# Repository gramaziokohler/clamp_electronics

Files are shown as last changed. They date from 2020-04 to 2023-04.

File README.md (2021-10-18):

# clamp_electronics
Electronics for remote controlled robotic actuators (clamps). 

This repo is part of the [Robotic Assembled Timber Structures with Integral Timber Joints](https://github.com/gramaziokohler/integral_timber_joints) project. 

## Repo folder structure

This repository hold the following files:

- **/xx_Description** - Eagle schematics and board designs for a specific controller design
- **/eagle_library** - stores custom eagle libraries from third-party or created by myself
- **/doc** - Electronics modules and other components documentation from original manufactures.

## Design Goals

The goal of the clamp controller is to be able to achieve the following high-level functions: 

- Communicate wirelessly with a radio base station
  - Receive commands
  - Report status
  - Report a jammed stop during move
- Control 1 or 2 motors for the clamp's main linear movement
  - Positional Control
  - Follow a trapezoidal motion profile
- Operate on 3 or 4-cell Li-Po Battery power
- Monitor jamming conditions of the clamp
- Monitor sensors (if any, such as loadcells)
- Monitor end / homing switch
- Monitor pneumatic autoswitch
- Monitor battery voltage

## Controller Design

Not all designs implemented the full list of design goals.

### [01_SerialController](/01_SerialController/01_SerialController.md)

This controller receives command from Serial Tx Rx pins.

Two load cell can be connected via two HX711 Analog-to_Digital Module.

The design supports two DC motors with *single* channel encoder. The shaft rotation direction is inferred from the direction of programmed movement. (This design is later proved to be imprecise)

### [02_RadioPIDController](02_RadioPIDController/02_RadioPIDController.md)

This controller interfaces the CC1101 radio directly via Hardware SPI on Arduino Nano. It can receive and respond to commands from either USB Serial or from the Radio.

The hardware and pin out supports two motors being PID controlled with two-channel encoder feedback.

### [03_RadioPIDControllerV2](03_RadioPIDControllerV2/03_RadioPIDControllerV2.md)

This controller is an improvement of the 02_RadioPIDController with the intent to improve the following aspects:

- Better DC power regulation to avoid digital blackout
- Ability to support a two-motor firmware or single-motor (with added features) firmware.
- 1 or 2 LED output with onboard series resistor

### [10_ESP32CAMAdapter](10_ESP32CAMAdapter/10_ESP32CAMAdapter.md)

This an adapter board for connecting AIThinker ESP32-CAM module.

## Sub-systems and Electronic Module Documentation

### Motor Driver

[Motor Driver XY160D](doc/motor_driver/motor_driver_XY160D.md)

This H-Bridge Bi-Directional MOSFET motor driver is chosen due to its high rated current (7A constant, 50A peak).  

- Other drivers such as L298N offers low output current (L298N only 2A constant output 3A peak per channel) 
- This driver has a simple IN1 + IN2 + ENA interface which is easy to interface. 
- PWM and Bidirectional operation is necessary for position control.

### Radio

[Details of CC1101 Radio Module](doc/radio/CC1101_Radio.md)

This CC1101 radio module is chosen because it is the most available sub-GHz packet based radio.

- The sub-GHz frequency is better at going around obstacles in a construction environment.
- ISM bands that are free to use.
- The highly integrated radio transceiver chip on a module is easy to use and interface. 
- Existing Arduino compatible library exists.

Radio frequency / channel / sync word and it's operation is controlled by software and are documented in firmware repo.

### MCU

The Arduino Nano (ATmega328 + new bootloader) is chosen for its small size, low cost and protoboard friendly pin layout. The Nano do not have a lot of IO available but is barely enough for a 2 motor controller.

[Arduino Nano V3 Pinout](http://lab.dejaworks.com/arduino-nano-pinouts/) ( [Arduino.cc Nano Page](https://store.arduino.cc/arduino-nano) )

### Load Cell

A 4-wire load cell can be used to dynamically measure the pull force of the actuator. Such load cell can be interfaced to the Arduino via a AD Converter designed for load cell measurement.

[Details of the HX711 Load Cell A/D Module](/doc/load_cell/load_cell.md)

The HX711 module was selected due to its compact size, low cost and ready-to-use library. Measuring frequency is 80Hz.

### Battery Voltage Regulation for controller

The fluctuating battery voltage for a 4-cell Li-Po is between 12.8V to 16.8V. This needs to be regulated to stable 5V DC for the digital circuitry.

[Details and calculation of LM7805 option](doc/voltage_regulation/linear_regulator.md)

### Battery Voltage Sense

[Details and calculation of voltage divider](doc/battery_sense/Battery_Voltage_Sensing.md)

### Battery Cable Harness

A Y cable is necessary to connect the Li-Po Battery to both the motor driver and the controller Battery. 

**Male XT60 Connector** at the battery side

**2x Female Phoenix Terminal Block Plug** (Phoenix 1757019 - MSTB 5.08 picth) at controller side.

------

## Peripheral Devices

The choice of DC motor and Li-Po Battery is flexible from the perspective of the controller electronics. As long as their specification is within allowable range defined below:

### DC Motor

The chosen DC motor should be rated 12V. Other ratings might work as long as overheat is not an issue and sufficient torque is produced.

### Hall Effect Sensor

Two phase hall effect shaft encoder should be used for positional feedback. The output of the encoder should ideally be 5V TTL logic. 

Should the motor have a gearbox, the shaft encoder should be attached to the motor shaft (not the gearbox output shaft) for better resolution.

Sensor resolution should be around 500 - 1000 steps per 1mm clamp linear output.

### Li-Po Battery

**4-cell** Li-Po battery is chosen for the following reasons:

- High power density for starting DC motor
- High energy density to save space and weight
- 14.8V - 16.8V voltage match well with 12V DC motor.

**1000mAh** or above for reasonable use time.

**XT60 Connector** is conventional

**Voltage Assumption for calculation**: We assume a fully charged 4-cell battery to have **16.8V (@4.2V)**, and stop using the battery at **14.8V (@3.7V)**  , although absolute minimum is **14.0V (@3.5V)**

Note: 3-cell battery will also operate fine but at reduced torque

Credits
-------------

This repository was created by Pok Yin Victor Leung <leung@arch.ethz.ch> [@yck011522 ](https://github.com/yck011522) at [@gramaziokohler](https://github.com/gramaziokohler)

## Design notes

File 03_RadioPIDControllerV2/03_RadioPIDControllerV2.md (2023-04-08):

# 03 Radio PID Controller V2

This controller is an upgrade of 02_Radio_PID_Controller and retains most of the design features of the previous controller with the following modifications:

- 5V power regulation is improved 
- LED connections and resistors are integrated
- Some bottom routing is redesigned for easier soldering.

## Design Goals

This clamp controller can achieve the following goal (with proper firmware):

- Control and communicate through CC1101 radio module. (SPI)
- Control 1 or 2 motors for the clamp's main linear movement
  - PWM / Bidirectional output via XY160D driver to two DC motors
  - Close loop feedback from two-phase hall effect shaft encoder from 2 motors
- Operate on 3 or 4-cell Li-Po Battery power
- Monitor homing switch / pneumatic autoswitch
- Monitor battery voltage
- Output for 1 or 2 LED status light

## Component choice

**Battery Choice:** Up to user (typical: 4-cell Li-Po 1000mAh 4S 75C)

**Radio Choice:** [CC1101 Module](../doc/radio/CC1101_Radio.md)

**Motor Driver Choice:** [Motor Driver XY160D](../doc/motor_driver/motor_driver_XY160D.md)

**MCU Choice:** Arduino Nano (ATMEGA328 with new bootloader)

**Voltage Regulation:** Single stage LM7805 solution (see schematic)

**Addressing / Settings DIP Switch:** 4 position DIP switch with resistor ladder

**End Switch Choice:** Normal close (NC) switch

## Schematic

[Eagle Schematic File](Controller.sch)

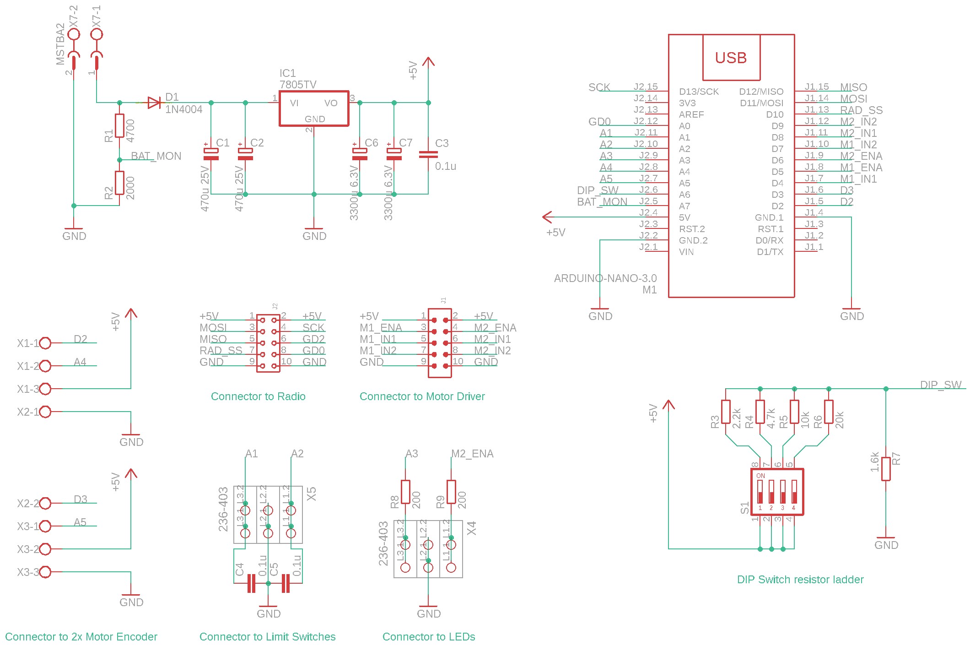
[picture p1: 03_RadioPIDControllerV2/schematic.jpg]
schematic


## Board

This board is built on **protoboard**, the following board shows mostly the hard wiring underneath the protoboard. There are jumpers that routes from top side not drawn here.

[Eagle Board File](Controller.brd)

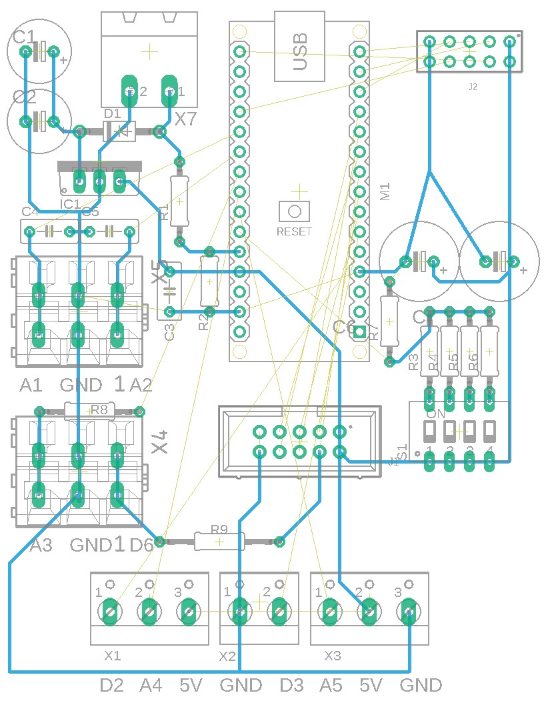
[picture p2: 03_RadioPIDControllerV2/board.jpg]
board


## Photo

The Controller in enclosed case with plugged in battery. The disconnected cables goes to DC motor with encoder.

Photo_WithCoverTop

------

Arduino Nano and radio module (Blue PCB with antenna) on protoboard. The Motor driver (red PCB) can be  seen below the protoboard. 

Photo_OffCover

## Arduino Pin Assignment

| | 1 motor operation | 2 motor operation |
| --- | --- | --- |
| Homing Switch | 1 switch (A1) | 2 switches (A1, A2) |
| Gripper Autoswitch | 1 input (A2) | not available |
| Motor Encoder 1 | interrupt (D2) | interrupt (D2, D3)  |
| Motor Encoder 2 | interrupt (D3) | gpio (A4, A5) |
| Motor Status LED (orange/red) | D6 | not available |

## Modification

During the third phase of the project the power regulation is modified. The LM7805 is removed and a LM2596 DC-DC converter module is placed in the same role.  This improved the regulation efficiency during standby mode and particularly important with the addition of the ESP32 CAM module. The ESP32 CAM draws substantial current and (confirmed by test) cannot be supported by the 7805, causing it to run into thermal protection. 

| Device | Current Draw @14.8V (LM7805) | Current Draw @14.8V (LM2596) |
| --- | --- | --- |
| Controller with No Radio | 0.055 | 0.1 |
| Controller with Radio | 0.056 | 0.116 |
| + ESP32 CAM | 0.1 | 0.23 |
| + ESP32 CAM LED On | 0.15 | 0.358 |

The new LM2596 module is not integrated to the same PCB but is wired off-board and is fixed with foam tape to the side of the worm gearbox.

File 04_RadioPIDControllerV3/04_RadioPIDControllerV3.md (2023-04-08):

# 04 Radio PID Controller V3

This controller is an upgrade of 03_Radio_PID_Controller and retains most of the design features of the previous controller with the following modifications:

- Arduino Mega 2560 PRO from robotdyn
- 1 channel Main Motor Control
- 2 channels Motor Control for gripper motors
- PCB base instead of hand-soldered 

## Design Goals

This clamp controller can achieve the following goal (with proper firmware):

- Control and communicate through CC1101 radio module. (SPI)
- Control 3 motors, 1 for the clamp's main linear movement, 2 for clamp gripper actuation
  - PWM / Bidirectional output via XY160D driver to two DC motors
  - Close loop feedback from two-phase hall effect shaft encoder from 2 motors
  - Main motor and gripper motor not not operate simultaneously. 
- Operate on 3 or 4-cell Li-Po Battery power
- Monitor homing switch / pneumatic autoswitch
- Monitor battery voltage
- Output for 1 or 2 LED status light

## Component choice

**Battery Choice:** Up to user (typical: 4-cell Li-Po 1600mAh 4S 75C)

**Radio Choice:** [CC1101 Module](../doc/radio/CC1101_Radio.md)

**Motor Driver (Main Screw Motor) Choice:** H-Bridge Motor Driver JZ3615 (15A continuous, 50A peak)

**Motor Driver (Pin Gripper Motor) Choice:** [H-Bridge Motor Driver L298HN](https://www.sparkfun.com/datasheets/Robotics/L298_H_Bridge.pdf) (Total 4A continuous)

**MCU Choice:** Arduino Nano (ATMEGA328 with new bootloader)

**Voltage Regulation:** Single stage LM7805 solution (see schematic)

**Addressing / Settings DIP Switch:** 4 position DIP switch with resistor ladder

**End Switch Choice:** Normal close (NC) switch

## Schematic

[Eagle Schematic File](Controller.sch)

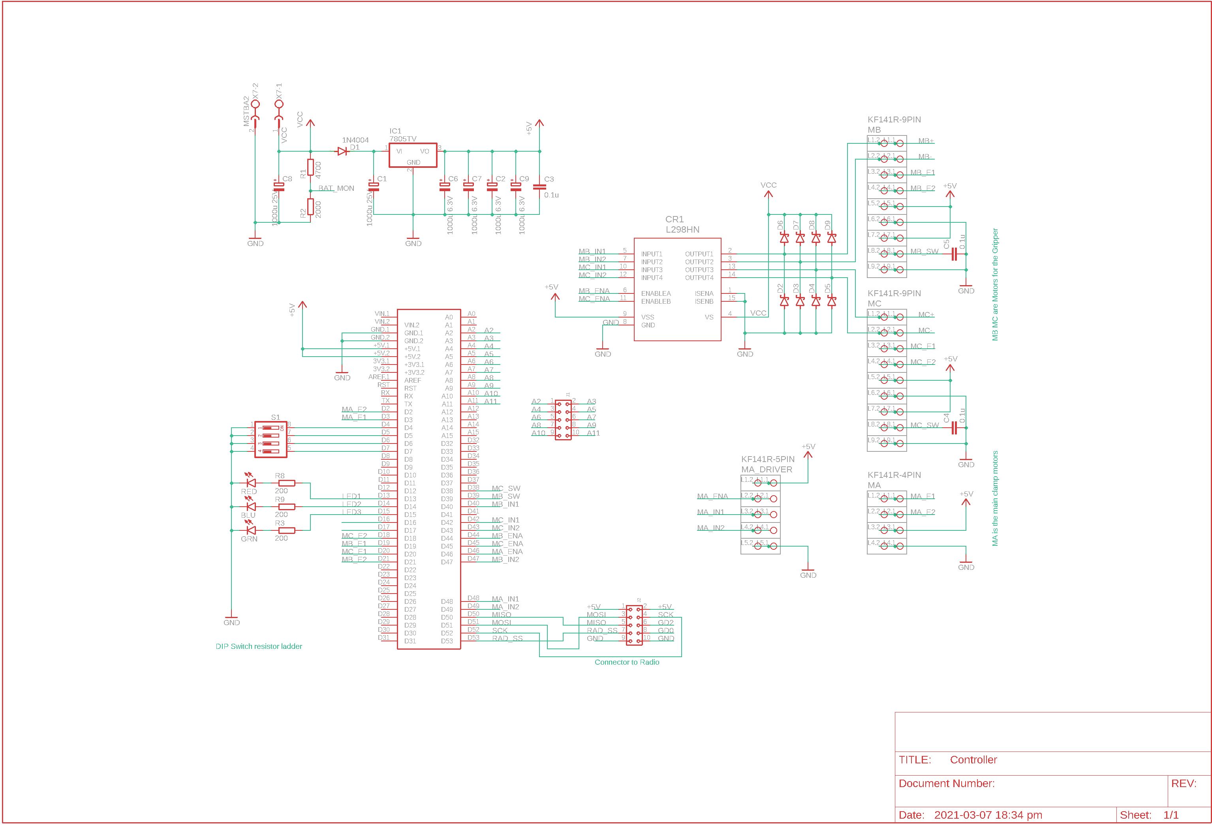
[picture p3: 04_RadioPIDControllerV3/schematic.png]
schematic


## Board

This board is built by PCB fab company in China, the following drawing shows bottom side (blue) and top side (red).

[Eagle Board File](Controller.brd)

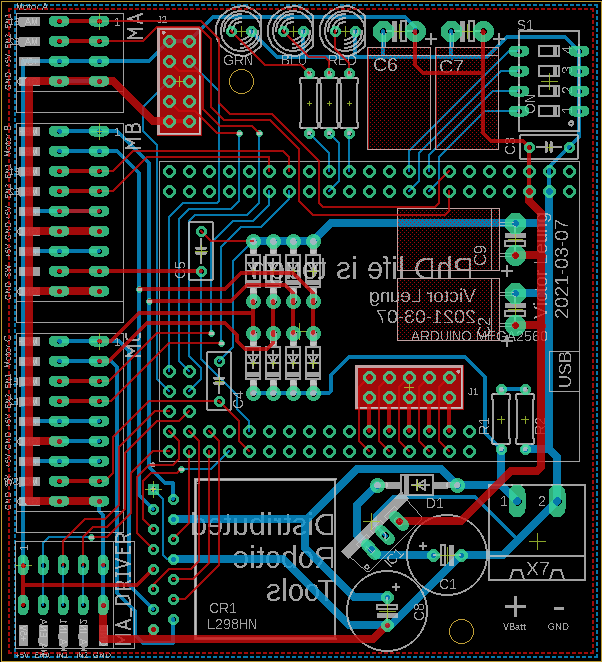
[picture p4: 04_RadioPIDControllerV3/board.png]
board


## Errata

- **BAT_MON** net should be connected to an Analog Pin on the MCU, but was not connected. This is rectified by jumper wire from trace between R1 R2 to J1 Pin **A3**.
-  **GD0** net (radio message arrive flag) should be connected to a pin on the MCU, but was not connected. This is rectified by jumper wire from J2 GD0 pin to J1 Pin **A2**.
-  Two buttons are added for manually controlling the grippers, they are wired to A96 A10 A11 

## Photo

The Controller in enclosed case with all cables connected.

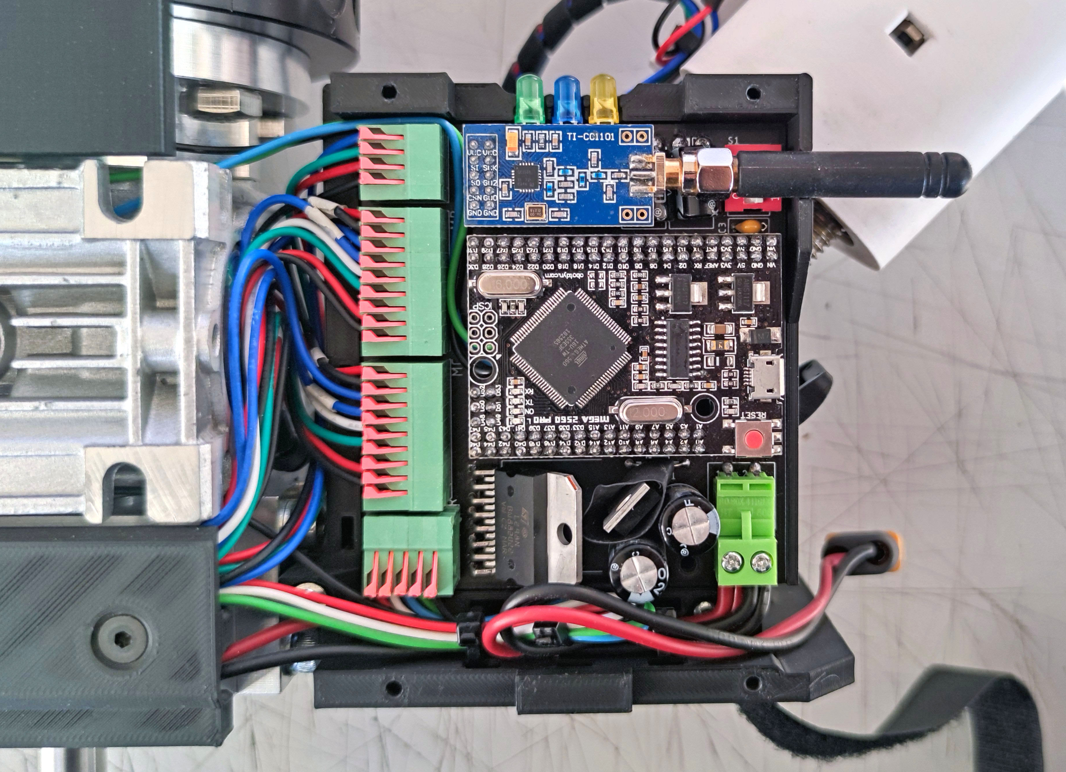
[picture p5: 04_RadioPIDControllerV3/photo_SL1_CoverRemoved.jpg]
photo_SL1_CoverRemoved


------

## Arduino Pin Assignment

| | MA (Screw Motor) | MB (Gripper Motor) | MC (Gripper Motor) |
| --- | --- | --- | --- |
| Motor IN1 | MA_IN1 (D48) | MB_IN1 (D40) | MC_IN1 (D42) |
| Motor IN2 | MA_IN2 (D49) | MB_IN2 (D47) | MC_IN2 (D43) |
| Motor Enable | MA_ENA (D46) | MB_ENA (D44) | MC_ENA (D45) |
| Motor Encoder 1 | MA_E1 (D2) interrupt 4 | MB_E1 (D19) interrupt 2 | MC_E1 (D20) interrupt 1 |
| Motor Encoder 2 | MA_E2 (D3) interrupt 5 | MB_E2 (D21) interrupt 0 | MC_E2 (D18) interrupt 3 |
| Homing Switch | nil | MB_SW (D39) | MC_SW(D38) |

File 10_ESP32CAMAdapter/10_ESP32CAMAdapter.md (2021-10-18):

# 10_ESP32CAMAdapter

This an adapter board for connecting AIThinker ESP32-CAM module.

The Camera Module draws power from the stabilized 5V supply of the Clamp controller. It does not communicate directly with the clamp controller. 

- A DIP switch is used to set the IP address of the Controller. 
- A Status LED indicates successful connection with the Wi-Fi Access Point.

The board is implemented on protoboard. The wire terminal is not present and is replaced with a directly soldered wire. The board have to be removed during programming. 

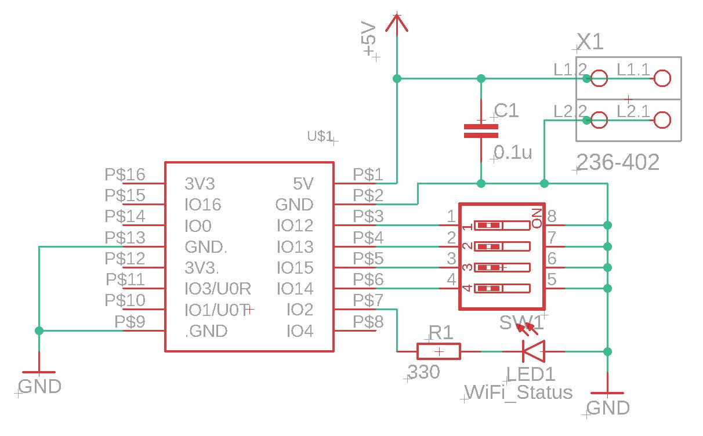
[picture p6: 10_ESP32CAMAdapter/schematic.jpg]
schematic


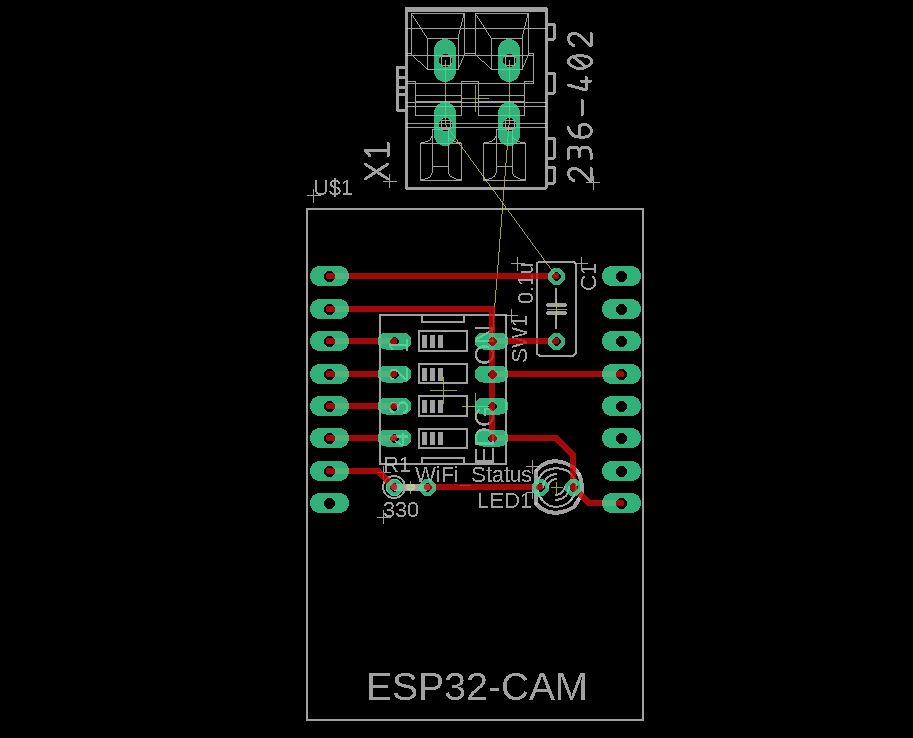
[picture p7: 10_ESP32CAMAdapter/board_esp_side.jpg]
board_esp_side


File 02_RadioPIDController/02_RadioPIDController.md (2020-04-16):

# 02 Radio PID Controller

This controller is put together in a rush for project Tokyo. Some components are drawn here, but not installed due to lack of on-hand components.

## Design Goals

This clamp controller can achieve the following goal (with proper firmware):

- Control and communicate through CC1101 radio module. (SPI)
- Control 1 or 2 motors for the clamp's main linear movement
  - PWM / Bidirectional output via XY160D driver to two DC motors
  - Close loop feedback from two-phase hall effect shaft encoder from 2 motors
- Operate on 3 or 4-cell Li-Po Battery power
- Monitor end / homing switch
- Monitor battery voltage
- Output for a LED status light or buzzer 

## Component choice

**Battery Choice:** Up to user (typical: 4-cell Li-Po 1000mAh 4S 75C)

**Radio Choice:** [CC1101 Module](../doc/radio/CC1101_Radio.md)

**Motor Driver Choice:** [Motor Driver XY160D](../doc/motor_driver/motor_driver_XY160D.md)

**MCU Choice:** Arduino Nano (ATMEGA328 with new bootloader)

**Voltage Regulation:** Single stage LM7805 solution (see schematic)

**Addressing / Settings DIP Switch:** 4 position DIP switch with resistor ladder

**End Switch Choice:** Normal close (NC) switch

## Schematic

[Eagle Schematic File](Controller.sch)

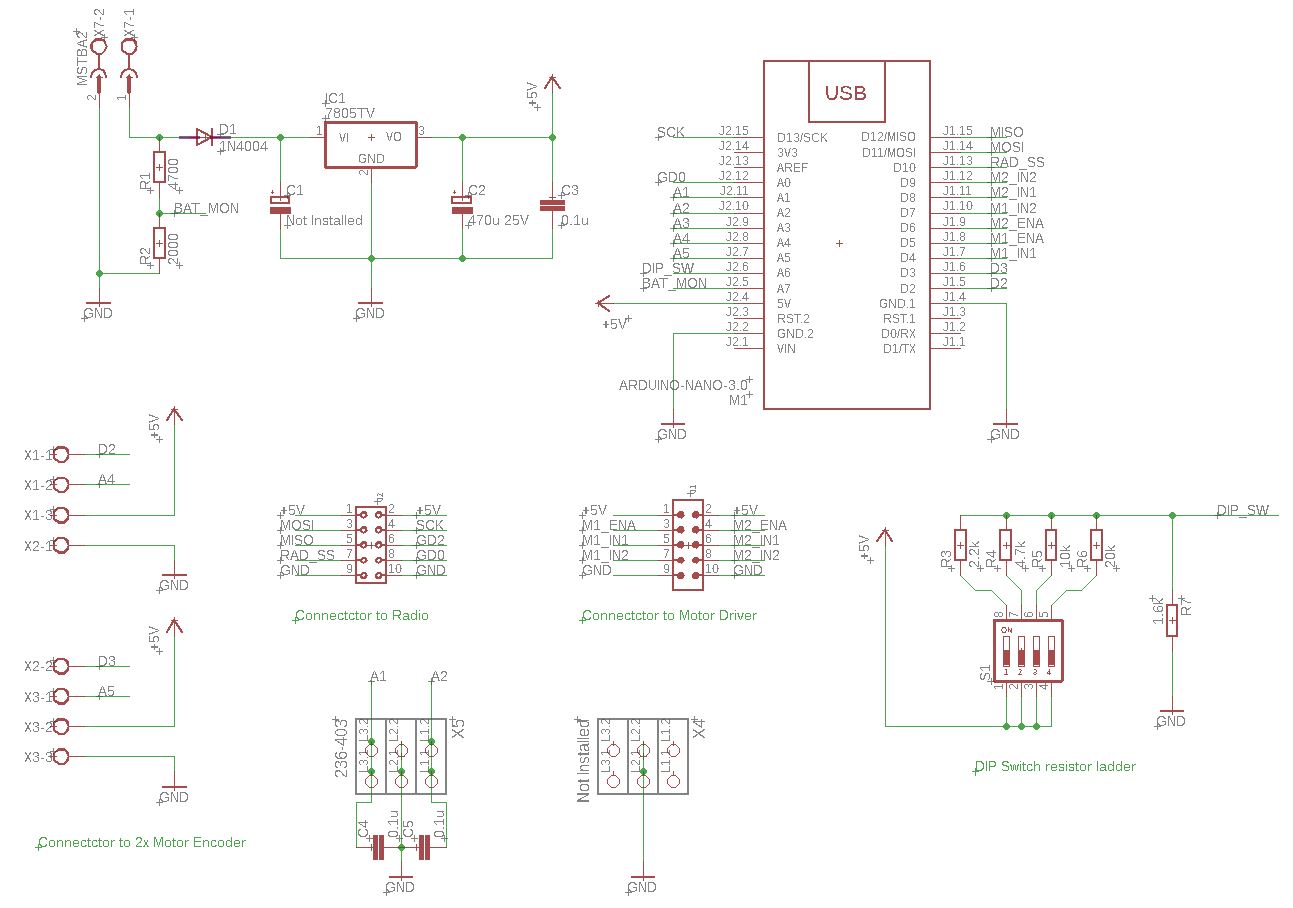
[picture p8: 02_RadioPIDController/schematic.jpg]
schematic


## Board

This board is built on **protoboard**, the following board shows mostly the hard wiring underneath the protoboard. There are jumpers that routes from top side not drawn here.

[Eagle Board File](Controller.brd)

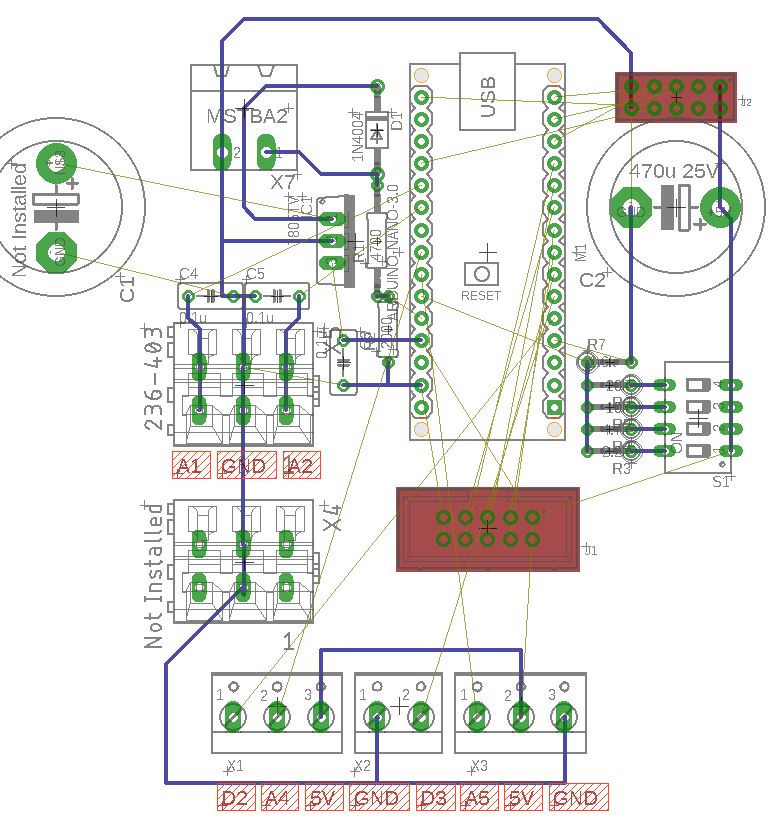
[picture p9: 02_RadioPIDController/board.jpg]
board


## Photo

The Controller in enclosed case with plugged in battery. The disconnected cables goes to DC motor with encoder.

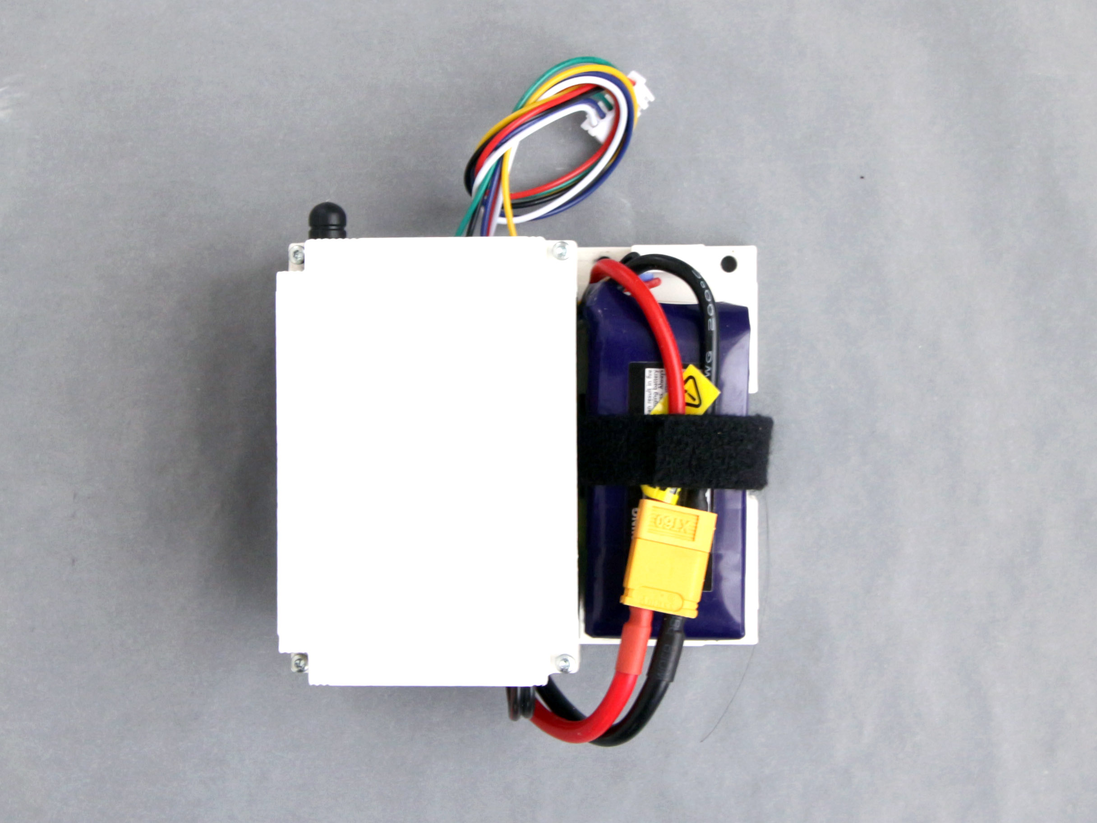
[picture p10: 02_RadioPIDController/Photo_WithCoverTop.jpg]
Photo_WithCoverTop


------

Arduino Nano and radio module (Blue PCB with antenna) on protoboard. The Motor driver (red PCB) can be  seen below the protoboard. 

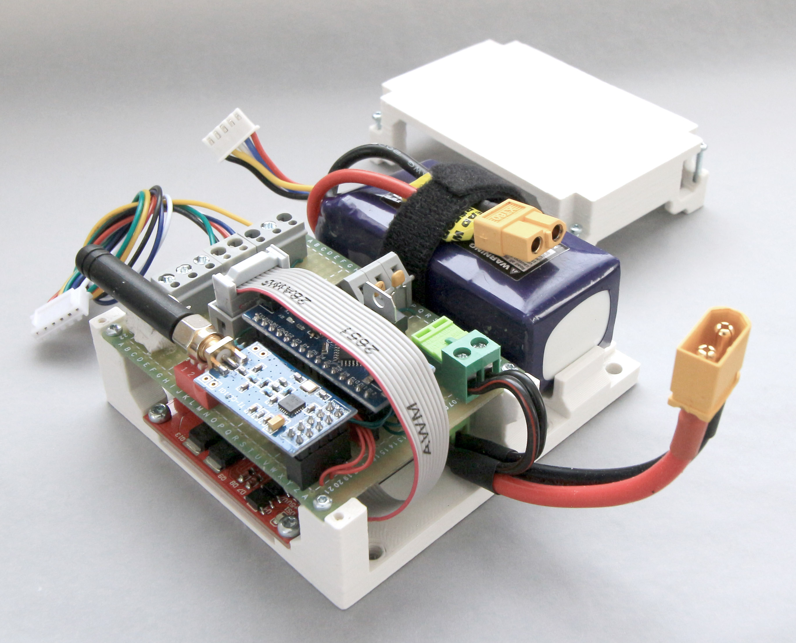
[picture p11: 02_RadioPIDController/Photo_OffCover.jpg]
Photo_OffCover


## Arduino Pin Assignment

The following header file can be used for pin assignment

(TODO)

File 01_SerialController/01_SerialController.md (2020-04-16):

# 01 Serial Controller

## Design Goals

This clamp controller can achieve the following goal (with proper firmware):

- Control and communicate through serial interface. 
  - From computer via **CH340 USB chip** on Arduino Nano
  - From Radio via **TX RX interface** with [USB Radio Dongle](../00_USBRadioDongle/00_USBRadioDongle.md)
- Control 1 or 2 motors for the clamp's main linear movement
  - PWM / Bidirectional output via XY160D driver to two DC motors
  - Close loop feedback from single-phase hall effect shaft encoder from 2 motors
- Operate on 3 or 4-cell Li-Po Battery power
- Monitor battery voltage

## Component choice

**Battery Choice:** Up to user (typical: 4-cell Li-Po 1000mAh 4S 75C)

**Radio Choice:** [00_USBRadioDongle](../00_USBRadioDongle/00_USBRadioDongle.md)

**Radio Interface:** TX RX Interface with 5V power

**Motor Driver Choice:** [Motor Driver XY160D](../doc/motor_driver/motor_driver_XY160D.md)

**Load Cell Interface:** [HX711 AD Module](../doc/load_cell/load_cell.md)

**Load Cell Choice:** Up to user (any 4 wire load cell)

**MCU Choice:** Arduino Nano (ATMEGA328 with new bootloader)

**Voltage Regulation:** Single stage LM7805 solution (see schematic)

**End Switch Choice:** No end switch is connected. (end position inferred by software)

## Schematic

[Eagle Schematic File](SerialController.sch)

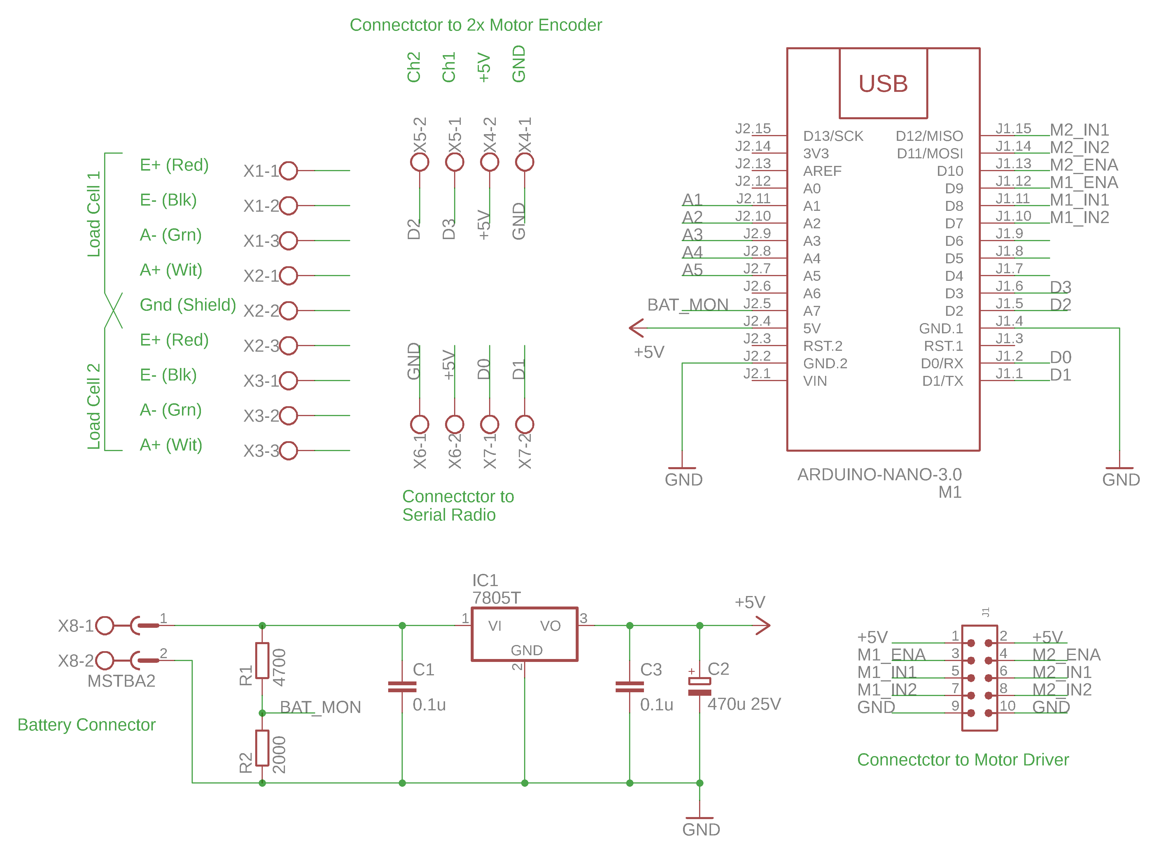
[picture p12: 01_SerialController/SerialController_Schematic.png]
SerialController_Schematic


## Photo

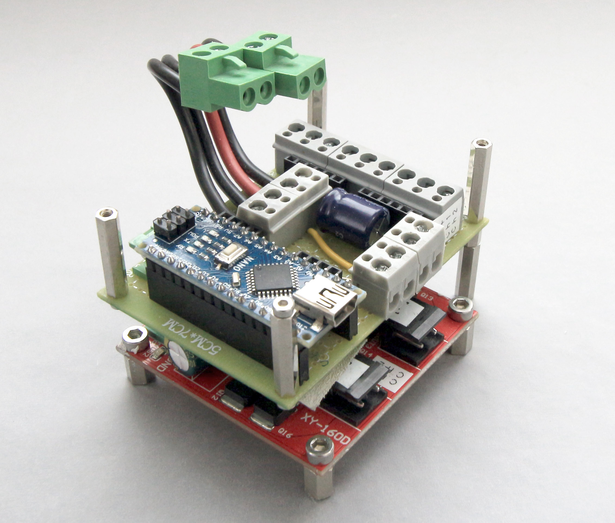
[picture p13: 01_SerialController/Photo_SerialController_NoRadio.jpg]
Photo_SerialController_NoRadio


## Test Notes

A simple test was performed to determine if the encoder has good repeatability. 

Result: Single-phase encoder is not reliable for bi-directional positional control. 

Inferring rotational direction is not reliable and result in poor axis repeatability.

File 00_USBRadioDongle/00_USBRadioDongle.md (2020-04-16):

# 00 USB Radio Dongle

This is a USB to CC1101 Radio dongle. 

[Details of CC1101 Radio Module and it's available frequency, mode and settings](../doc/radio/CC1101_Radio.md)

## Design Goals

This clamp controller can achieve the following goal (with proper firmware):

- Allow a PC to connect to it via USB. 
- Allow the PC to configure the CC1101 settings via the USB (address, frequency, channel and sync word)
- Allow the PC to send and receive variable length message packet via the USB
- Allow debug messages to be printed to a 1602 LCD Screen (via I2C bus with the PCF9574 IO Expander)

This radio is intended to be use as a **modular building block** for the network of remote-controlled clamps. It can be used on the master mode (PC) and the slave nodes (e.g. [01_SerialController](..\01_SerialController\01_SerialController.md)). However, later slave node controller (e.g. [02_RadioPIDController](..\02_RadioPIDController\02_RadioPIDController.md)) have integrated the radio control directly on the controller MCU, omitting the need for this dongle, saving an Arduino Nano and space. 

## Component choice

**Radio Choice:** [CC1101 Module](../doc/radio/CC1101_Radio.md)

**MCU Choice:** Arduino Nano (ATMEGA328 with new bootloader)

**Power:** Powered by host computer USB Port @ 5V

**Connector to 01 Serial Radio :** Phoenix Terminal Block Socket 5.08mm Pitch

**Connector to IC LCD Screen:** Reichelt PS Series 2.5mm Pitch 5 Pin PCB Connector (PS25/5G BR)  

## Schematic

[Original Eagle Schematic File](Dongle.sch)

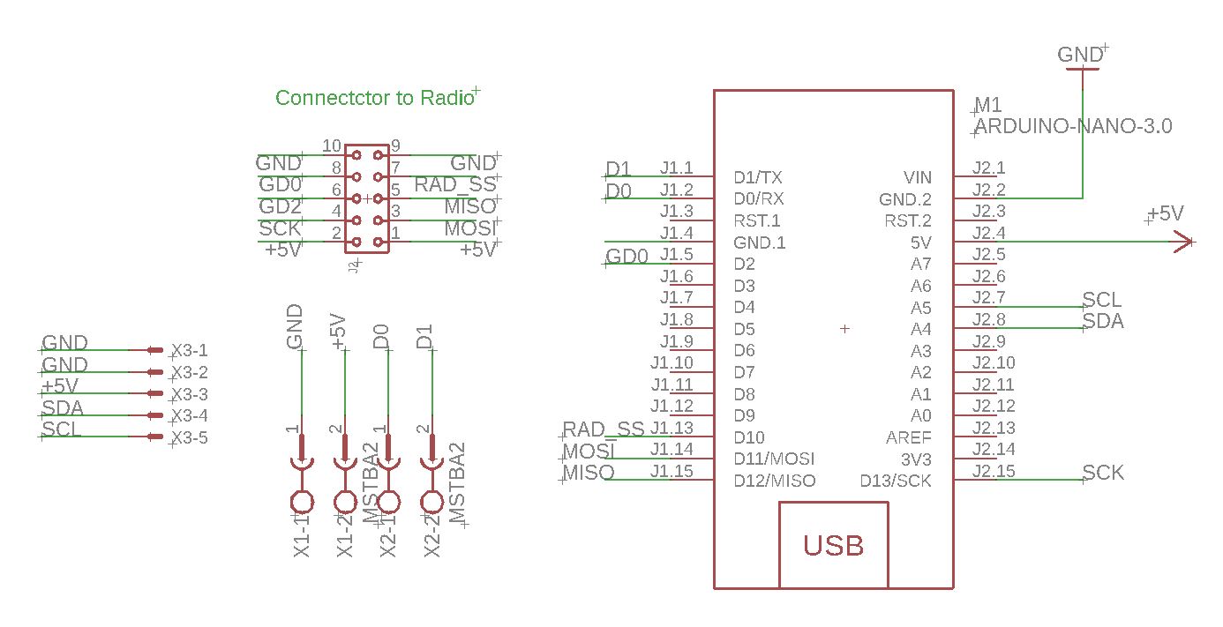
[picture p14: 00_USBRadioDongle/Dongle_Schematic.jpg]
Dongle_Schematic


## Board

This board is built on a 50mm x 70mm **protoboard**. The wiring is mainly completed using small wires. Arrangement of the components can refer to the photo below. The schematic drawing is also drawn with the connectors oriented the same as in the PCB.

## Photo

The Arduino Nano and CC1101 radio module can be seen. Mounted to a plastic case.

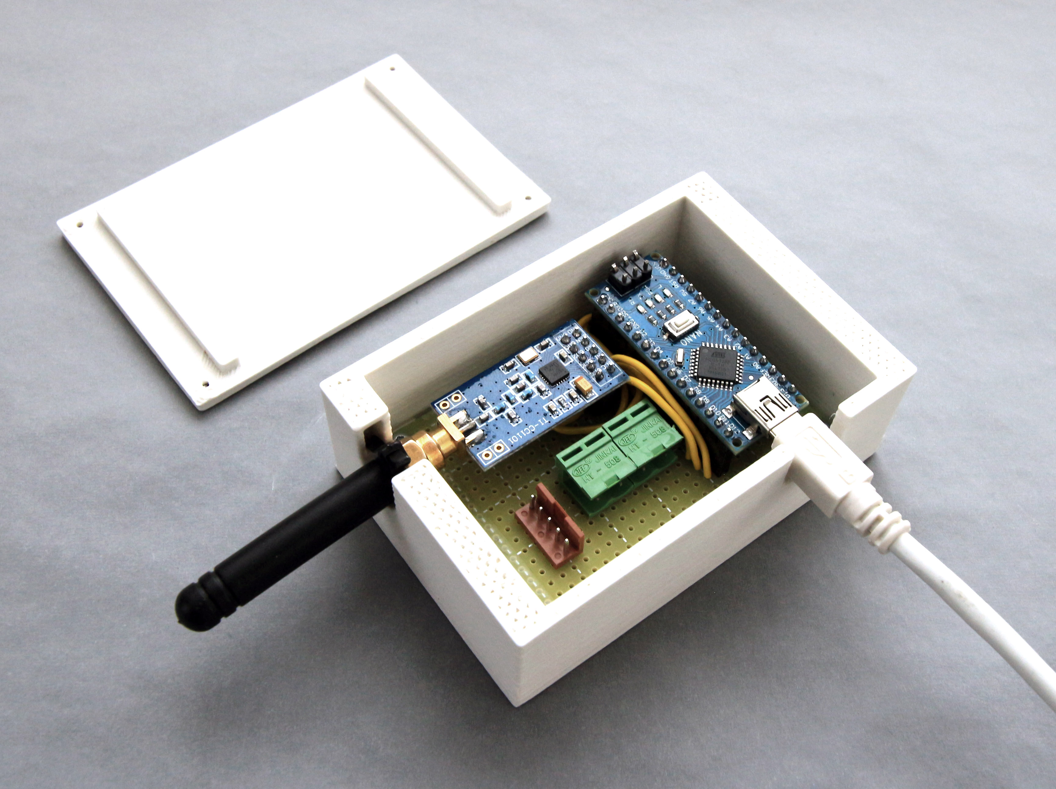
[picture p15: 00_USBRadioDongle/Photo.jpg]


------

Radio with case cover closed.

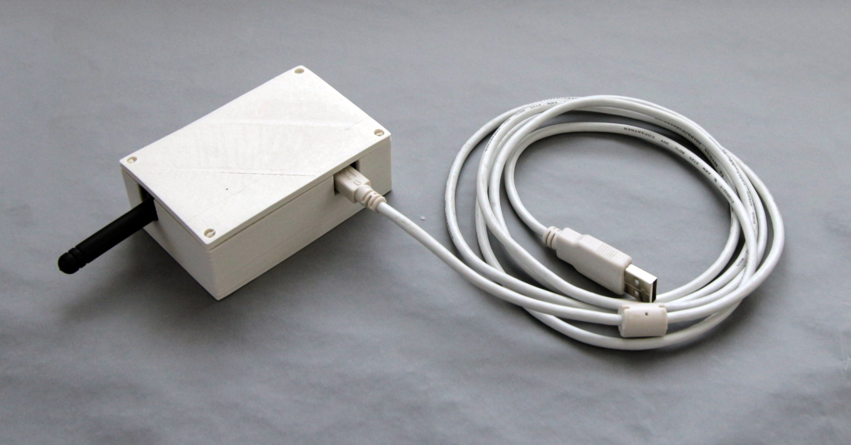
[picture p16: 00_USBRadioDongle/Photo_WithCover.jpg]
Photo_WithCover


## Firmware

Please see the serial_radio section in the [clamp_firmware repo](https://github.com/gramaziokohler/clamp_firmware).

## Arduino Pin Assignment

To the CC1101 radio module

| Radio Pin | Arduino Pin | Note |
| --- | --- | --- |
| 5V+ | 5V+ | |
| GND | GND | |
| CSN | D10 | Radio Slave Select |
| MOSI | D11 | MOSI Data |
| MISO | D12 | MISO Data |
| SCK | D13 | Serial Clock |
| GD0 | D2 | Message Arrival Indication |

------

To the dubug LCD screen

| LCD Screen Pin | Arduino Pin | Note |
| --- | --- | --- |
| Vcc | 5V+ | |
| GND | GND | |
| SDA | A4 | Serial Data  |
| SCL | A5 | Serial Clock |

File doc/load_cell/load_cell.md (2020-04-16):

# HX711 Load Cell A/D Module

There are different HX711 module on the market. Notably the Sparkfun version and this brand-less version. Note that pin arrangement is not identical. 

I choose this brand-less option simply because of lower cost.

HX711_module

## Specification of HX711

 [Data Sheet of Avia Semiconductor HX711](HX711.pdf)

**Resolution:** 24bit

**Measurement frequency:**10Hz / 60Hz (selectable)

## Pin Connection

Between Arduino and HX711 module:

| Label on module | Arduino Pin | Notes |
| --- | --- | --- |
| VCC | +5V | Power |
| GND | GND | Power |
| DT | Software SPI (Any IO Pin) | SPI Data  |
| SCK | Software SPI (Any IO Pin) | SPI Clock |

____

Between HX711 module and load cell:

| Label on module | Load Cell Wire | Cable Color (most of the time) |
| --- | --- | --- |
| E+ | Excitation + | Red |
| E- | Excitation - | Black |
| A- | Amplifier - | Green |
| A+ | Amplifier + | White |
| B- | Not Connected  | |
| B+ | Not Connected  | |
| GND | Shield | Wire or foil shield |

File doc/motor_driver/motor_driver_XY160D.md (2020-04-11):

# XY-160D motor driving board

**Motor Power Input Voltage** DC 6.5V - 27V

**Digital Power Input Voltage** DC 5V

**Number of Channels:** 2

**Max continuous output current:**  7A (Per Channel)

**Peak output current**: 50A

**PWM frequency range** 0-10 kHz (PWM signal at ENA input is used to regulate speed)

**Minimum pulse width:** 5us.

**Control signal Level (Compatible 3.3V/5V)**

**Logic High (H):** DC 3.0 ~ 6.5V

**Logic Low (L):** DC0 ~ 0.8V

| Pin Function | Label | Connection |
| --- | --- | --- |
| Drive Power Input +ve | 9-24V | Battery Positive |
| Drive Power Input -ve | PGND | Battery Negative |
| Power Output - Channel 1 +ve | OUT1 | Channel 1 Motor +ve |
| Power Output - Channel 1 -ve | OUT2 | Channel 1 Motor -ve |
| Power Output - Channel 2 +ve | OUT3 | Channel 2 Motor +ve |
| Power Output - Channel 2 -ve | OUT4 | Channel 2 Motor -ve |
| Digital Power Input +ve | +5V | Arduino 5V |
| Digital Power Input -ve | GND | Arduino Ground |
| Digital Input - Channel 1 - 1 | IN1 | Arduino GPIO |
| Digital Input - Channel 1 - 2 | IN2 | Arduino GPIO |
| Digital Input - Channel 2 - 1 | IN3 | Arduino GPIO |
| Digital Input - Channel 2 - 2 | IN4 | Arduino GPIO |
| Digital Input - Channel 1 Speed | ENA (near IN1) | Arduino GPIO (PWM)  |
| Digital Input - Channel 2 Speed | ENA (near IN3) | Arduino GPIO (PWM)  |

Note: Motor +ve and -ve denote when the motor spins according to Right Hand Rule. (a.k.a. CCW when viewed from output end.)

## Control Truth Table

| ENA  | IN1  | IN2  | OUT1 OUT2 Effect |
| ---- | ---- | ---- | --- |
| x | L | L | Short (Breaking) |
| x | H | H | Isolate |
| PWM  | H | L | Rotate (TODO: OUT1 > OUT2 ?) |
| PWM  | L | H | Rotate (TODO: OUT1 > OUT2 ?) |

## Connection to Motor 

Out 1 / Out 3 -> Motor +ve Lead

Out 2 / Out 4 -> Motor -ve Lead

## **Physical**

**PCB Size**  55x55x16mm  

**Mounting hole size**  3mm

**Weight** 32g

## Purchase

双路直流电机驱动板模块工业级马达正反转PWM调速L298逻辑7A160W

https://detail.tmall.com/item.htm?id=545415074433&spm=a1z09.2.0.0.32392e8dqyPg5S&_u=jl5jjmhde86 

## PDF

[XY160D_7A_160W_MotorDriver.pdf](XY160D_7A_160W_MotorDriver.pdf)

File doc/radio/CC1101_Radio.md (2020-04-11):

# CC1101 Radio Module

CC1101 is a [Low-power Sub-1 GHz wireless transceiver from Texas Instruments](http://www.ti.com/product/CC1101). 

> CC1101 is a low-cost sub-1 GHz transceiver designed for very low-power wireless applications. The circuit is mainly intended for the ISM (Industrial, Scientific and Medical) and SRD (Short Range Device) frequency bands at 315, 433, 868, and 915 MHz, but can easily be programmed for operation at other frequencies in the 300-348 MHz, 387-464 MHz and 779-928 MHz bands.
>
> The RF transceiver is integrated with a highly configurable baseband modem. The modem supports various modulation formats and has a configurable data rate up to 600 kbps.
>
> CC1101 provides extensive hardware support for packet handling, data buffering, burst transmissions, clear channel assessment, link quality indication, and wake-on-radio.
>
> The main operating parameters and the 64- byte transmit/receive FIFOs of CC1101 can be controlled via an SPI interface. In a typical system, the CC1101 will be used together with a microcontroller and a few additional passive components.
>
> The CC1190 850-950 MHz range extender [21] can be used with CC1101 in long range applications for improved sensitivity and higher output power.

There are many CC1101 modules from various manufacturers that have integrated peripheral components (mostly SMD) into a THT package with 2.54 pin spacing. 

I choose to use this particular version because it is available to me via Telesky Taobao shop. Other models may also work with some pin adaptation.

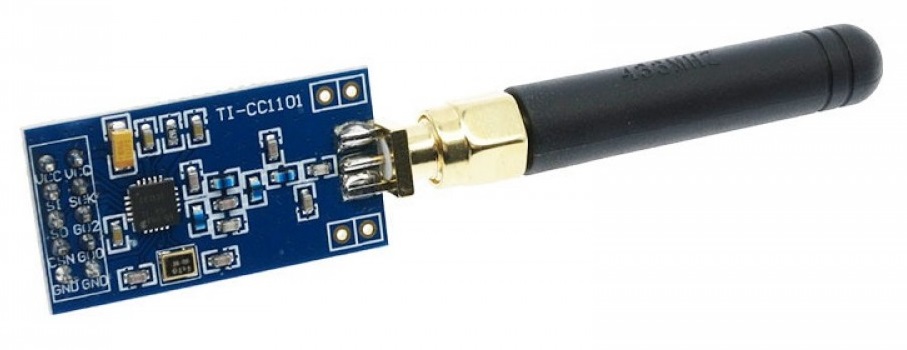
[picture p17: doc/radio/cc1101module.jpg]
cc1101module


The Pin out of the 

## Spec Sheet

[CC1101 Texas Instrument Datasheet](CC1101.pdf)

[CC1101 Module by Elechouse Datasheet](cc1101module_elechouse.pdf)

[CC1101 Module by SecuriPi Datasheet](cc1101module_securipi.pdf)

## Pinout Connection

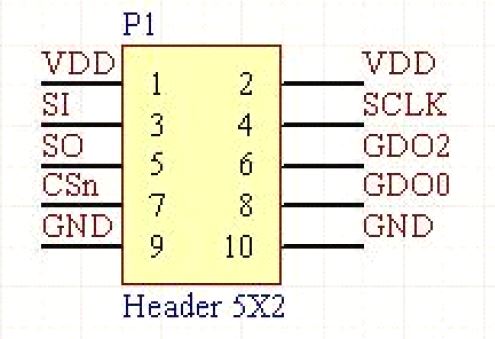
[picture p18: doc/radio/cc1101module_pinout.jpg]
cc1101module_pinout


Note: SI, SO, CSn, SCLK pins are part of the SPI bus and should be connected to the Arduino Hardware SPI pins. On the Nano, the pins assignments are as follows:

| CC1101 Module Designation | Arduino Designation | Arduino Pin Number |
| --- | --- | --- |
| SI | MOSI | D11 |
| SO | MISO | D12 |
| CSn | SS | D10 |
| SCLK | SCK | D13 |

GDO0 can be used for detecting incoming packages. It can be connected to any GPIO on Arduino.

## Voltage

In various documentation I have found (Including the official TI1101 doc and various module manufacturer). **The Vcc voltage is recommended to be 3.3V.**

However, I simply have no luck running the module at 3.3V from the Arduino. 

The Arduino 3.3V should provide 50mA and that should be enough current for the CC1101 at about 35mA max draw (at TX max power). I tried using 5V for Vcc and it all worked fine. So **I'm using 5V** now without investigating further.

I'm not sure if this particular module incorporated a regulator on board, does not look like so (from reading the SMD components because detailed schematic of the module is not found). 

All the other pins (SPI and SDO pins) are documented to be 5V tolerant and they can be directly connected to Arduino.

## Software Libraries

Further details of software is documented in the firmware repo.

https://github.com/pkarsy/mCC1101

https://github.com/pkarsy/CC1101_RF

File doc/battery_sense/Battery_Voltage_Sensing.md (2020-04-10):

# Battery Voltage Sensing

Battery voltage is monitored with one of the analog input on Arduino via a voltage divider.

Below is a divider schematic showing R1 and R2.

voltage_divider

## Calculation

Voltage Divider Calculation: http://www.ti.com/download/kbase/volt/volt_div3.htm (E24 values)

| LiPo Cells | Charged Voltage | Empty Voltage | R1 (Ω) | R2 (Ω) | Power Diss @ Charged Voltage (mW) | Converted Voltage |
| --- | --- | --- | --- | --- | --- | --- |
| 1 | 4.2 | 3.7 | 0 | x | 0 | |
| 2 | 8.4 | 7.4 | 680 | 1000 | 42 | 5.0 |
| 3 | 12.6 | 11.1 | 5100 | 3300 | 19 | 4.95 |
| 4 | 16.8 | 14.8 | **4300** | **1800** | 46 | 4.96 |
| 4 | 16.8 | 14.8 | **4700** | **2000** | 42 | 5.01 |

Note: The bold values can be used.

Empty battery has about 3.7/4.2 88% of the fully charged voltage. With the 1024 steps AnalogRead() on Arduino ADC, the **theoretical resolution of the capacity measurement is 121 steps.**

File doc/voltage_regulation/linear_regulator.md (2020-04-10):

# Battery Voltage Regulation for Controller

The fluctuating battery voltage for a 4-cell Li-Po is between 12.8V to 16.8V. This needs to be regulated to stable 5V DC for the digital circuitry.

## Calculation

**Max Input Voltage :** 16.8V
**Max Voltage Drop:** 16.8V -  5V = **11.8V**
**Current draw** is expected/measured to be about **0.2A**
**Max Power Dissipation:** 0.2 * 11.8V = **2.36W**

Although linear regulation is not efficient, LM78 series is ease and compact to use. Use TO-220 package for optimal heat dissipation. 

[LM7805CT (TO-220) Spec PDF](http://www.ti.com/lit/ds/symlink/lm340.pdf)

## Anti backflow diode

A diode is placed between the battery input and the regulator circuit. This prevents instantaneous high current draw from the motor driver to drain the first buffering capacitor. This design can can only avoid short power disruption.

Assuming a 0.2A current draw, an interruption of 0.1sec will demand the buffering capacitor to deliver **0.02C charge**.

Lowest Voltage at Capacitor is 14.8 when battery is about to go empty. The minimum input voltage of 7805 is 7V. Therefore the capacitor need to have a capacitor of 0.02C / (14.8-7V) = **2564 μF**

A **3300 μF capacitor** will be reasonable.

The assumption of 0.1s interruption is not tested, real application may have longer interruption. 

## Three linear regulation solutions below

Single stage LM7805 is the simplest, but heat is concentrated on one device and noise filtering may not be ideal.

Two stage LM7808 + LM7805 to share heat and better noise decoupling.

Two stage RC Buffer + LM7805 for simple design yet still provide better noise decoupling. The 20 Ohm resistor will dissipate about 0.8W (0.2A * 4V drop) of heat.

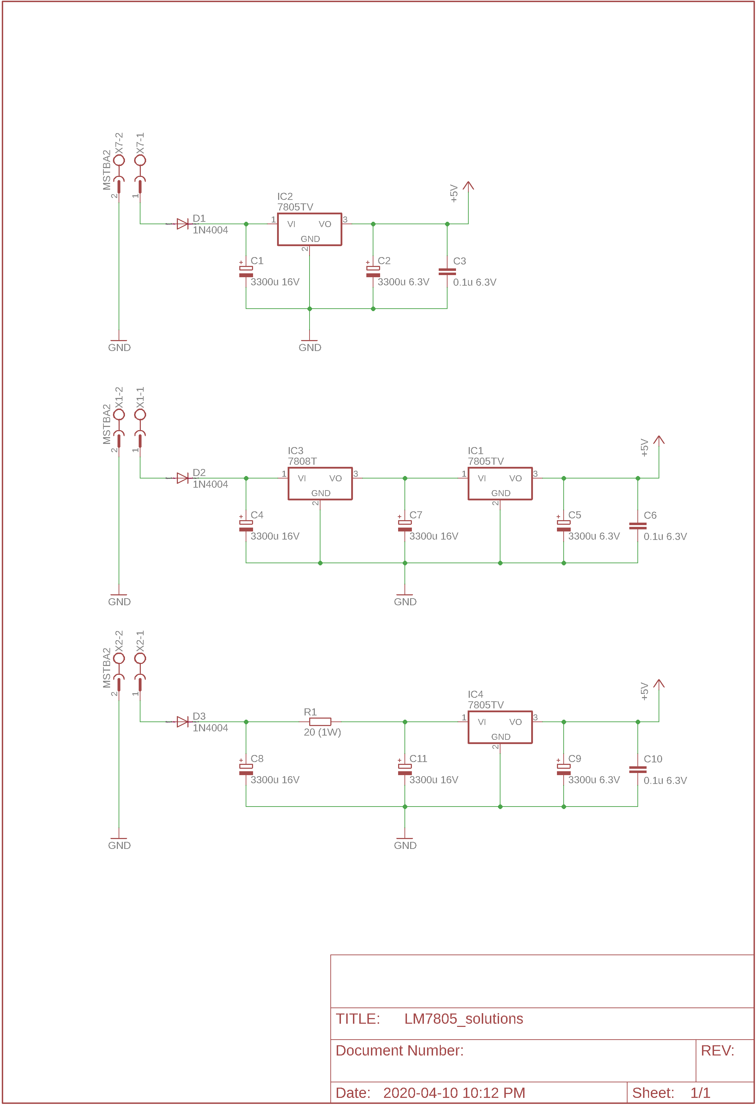
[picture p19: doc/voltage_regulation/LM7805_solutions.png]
LM7805_solutions


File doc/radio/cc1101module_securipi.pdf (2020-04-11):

## Use a CC1101 Radio module with a Raspberry Pi

Our previous PDF for Raspberry Pi showed you how to reverse engineer wireless gadgets that use the 433.92MHz AM frequency with OOK signalling, so you can learn codes sent by inexpensive wireless remote contols, and then use those codes to have your Raspberry Pi turn mains sockets on and off using a timer Python script on the Pi. If that sounds like what you want to do, you can read that PDF at http://www.securipi.co.uk/remote-433-receivers.pdf

The CC1101 radio modules have several advantages over the fixed 433.92MHz OOK receivers:

1. Send and receive on 315MHz, 433MHz, 868MHz and 915MHz ISM frequencies.
2. Support for 2-FSK, GFSK, ASK/OOK, 4-FSK & MSK modulation schemes.
3. External RP-SMA antenna socket. So it’s simple to add Yagi antennas for long distance comms.
4. Much of the signal processing is done on the radio boards for us, so less processor intensive.

The CC1101 boards we used are available for as little as £3.50 each on eBay UK. You’ll need a pair of CC1101 boards and two Raspberry Pi’s to follow this guide.

The boards attach to the SPI pins on the Pi:

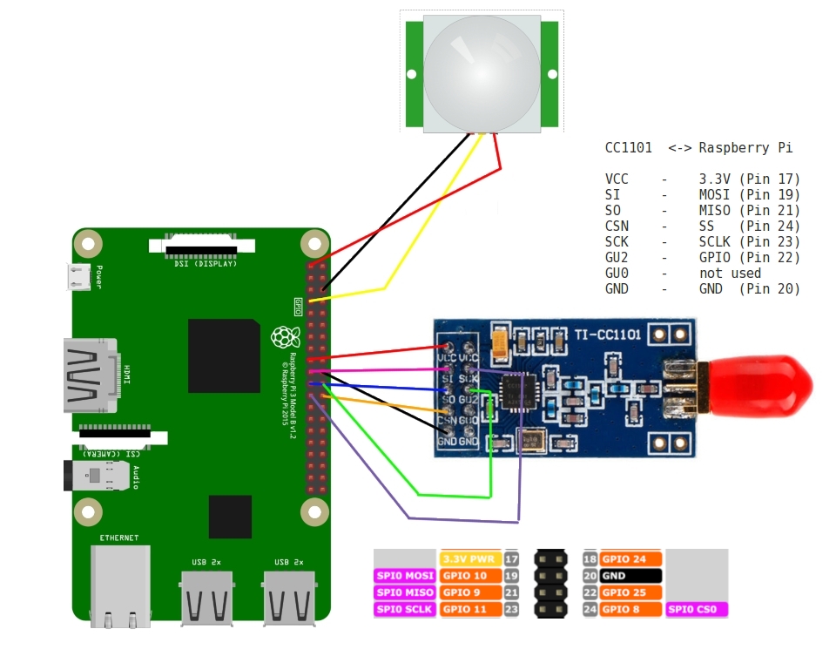
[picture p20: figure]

We bought our CC1101 boards from eBay for £3.22/$5 each including the SMA antennas: https://www.ebay.co.uk/itm/252616019027

You can attach the CC1101 board to the Pi using regular female to female breadboard cables, or you can use a PCB adapter, like this:

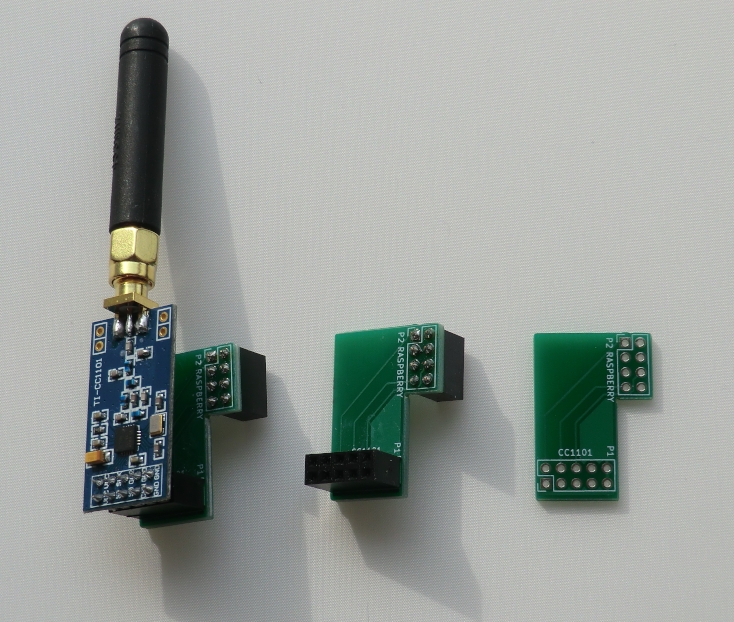
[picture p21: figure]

You can get the Gerber files to order your own PCBs from: https://github.com/salmg/CC1101/tree/master/schematic

Make a zip file from them and upload it to https://www.seeedstudio.io/fusion_pcb.html
and you can get 10 PCBs for $4.90 + $10 P&P, delivered in around 14 days.

You can get the 5x2 and 4x2 headers from eBay: https://www.ebay.co.uk/itm/382095134487

When the adapter is attached to the Pi you should be able to see 8 free pins either side of it.

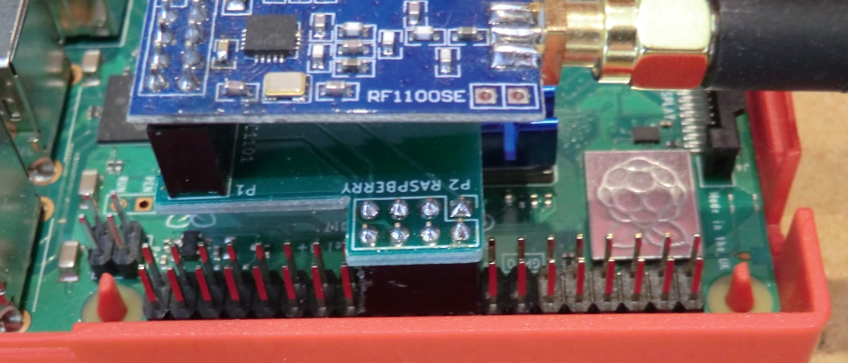
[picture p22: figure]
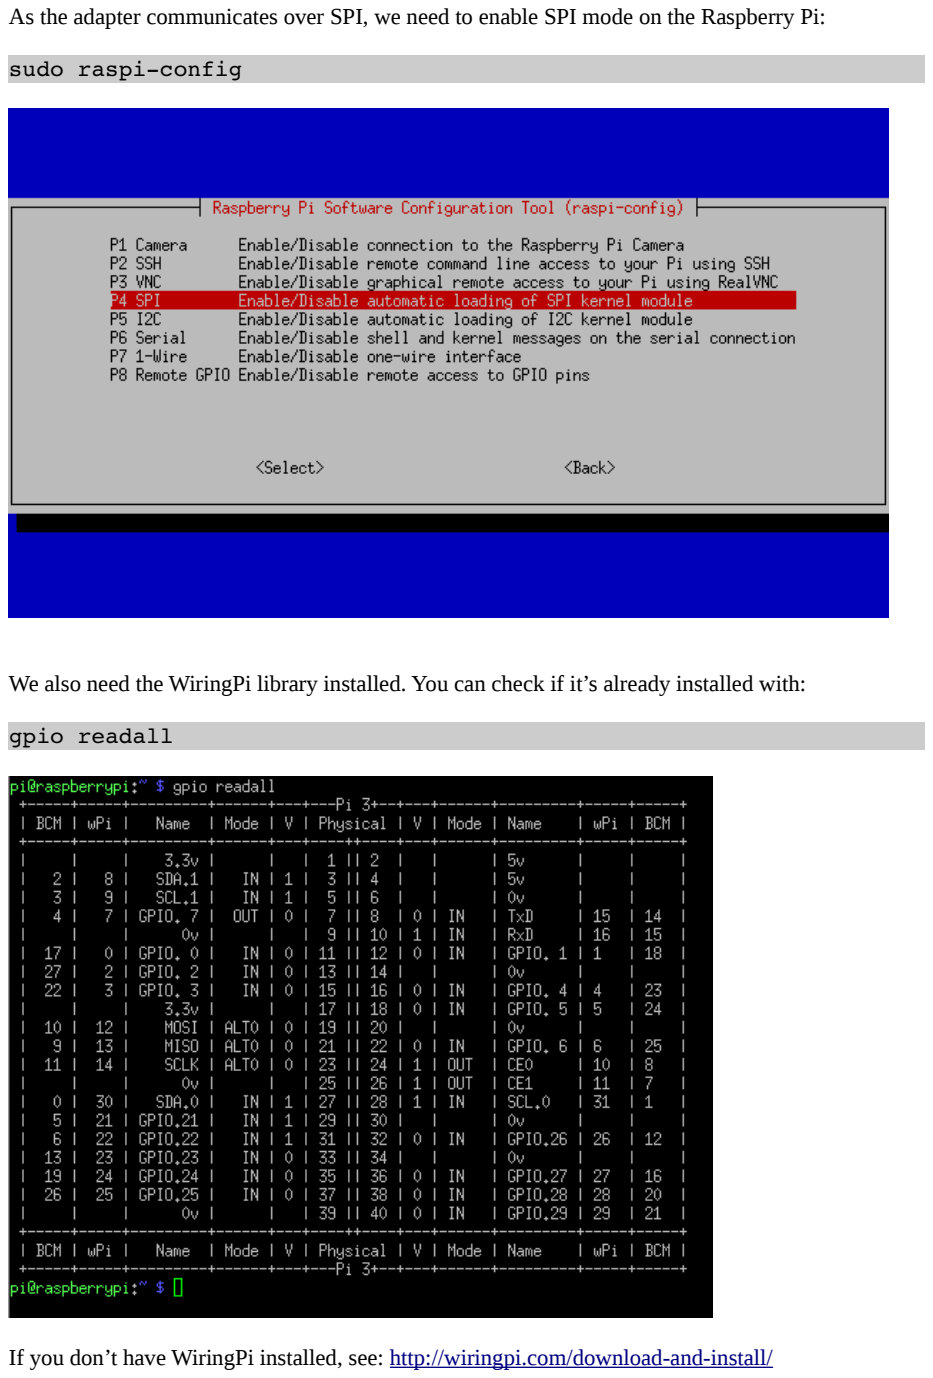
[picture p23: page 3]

As the adapter communicates over SPI, we need to enable SPI mode on the Raspberry Pi:

sudo raspiconfig

We also need the WiringPi library installed. You can check if it’s already installed with:

gpio readall

If you don’t have WiringPi installed, see: http://wiringpi.com/download-and-install/

Now we have SPI mode enabled and have WiringPi installed, we still need some software to drive the CC1101 boards.

The best software to use can be found at this Github page: https://github.com/SpaceTeddy/CC1101

The readme file at the Github page covers basic installation and testing of the RX_Demo (receiver) and TX_Demo (transmitter) scripts. This is exactly how we installed and configured it on both machines:

sudo aptget install gitcore
git clone https://github.com/SpaceTeddy/CC1101
cd CC1101
cp ~/CC1101/examples/raspi/*.cpp ~/CC1101

Then on the machine that’s going to be the transmitter:

sudo g++ lwiringPi TX_Demo.cpp cc1100_raspi.cpp o TX_Demo sudo chmod 755 TX_Demo

sudo ./TX_Demo v a1 r3 i1000 t5 c1 f434 m100

On the machine that will act as the receiver:

sudo g++ lwiringPi RX_Demo.cpp cc1100_raspi.cpp o RX_Demo sudo chmod 755 RX_Demo

sudo ./RX_Demo v a3 c1 f434 m100

If that worked you should now see packets going over-the-air between the two Pi’s, like this:

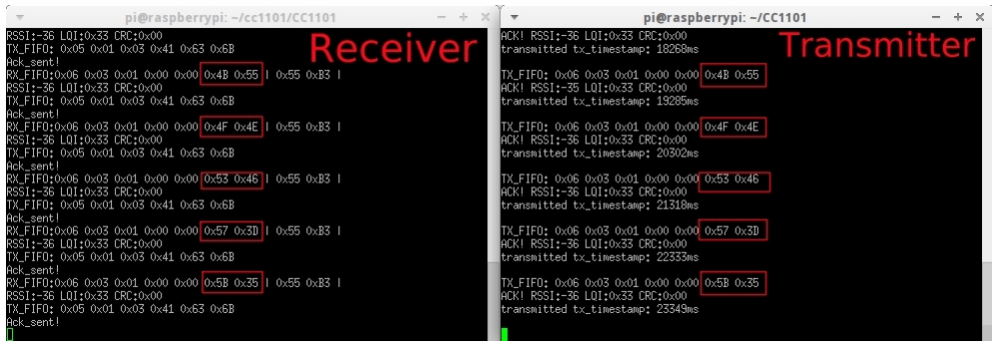
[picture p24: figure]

Because the boards can work with a wide range of different frequencies, modulation schemes and data rates, they are configured by sending a matching configuration block to each radio over SPI. Once each radio is setup in the same configuration, it’s just a case of transmitting a data packet burst on one radio and reading the receive buffer on the other radio.

The RX and TX demo files are great, but they don’t do anything really useful for us. In the next examples I’ll show you how to attach a PIR to the transmitter Pi, and store times and dates the PIR is triggered in a logfile on the receiver Pi.

You can download our own demos to both your Pi’s with:

wget securipi.co.uk/cc1101.zip
unzip cc1101.zip
ls

Here’s the list of files downloaded & what they do:

TX_DemoPir.cpp | Transmits a PIR2 message whenever the PIR detects movement
RX_DemoPir.cpp | Receives a signal and prints “PIR2 Triggered” to console.
RX_DemoPir2.cpp as above, with time and date logging to file test.txt
RX_DemoPir4.cpp as above, but also flashes an LED connected to GPIO4 when PIR triggered

Each of the cpp files are source code which needs to be compiled in the same way as the other demos. So for example, to use TX_DemoPir.cpp

sudo g++ lwiringPi TX_DemoPir.cpp cc1100_raspi.cpp o TX_DemoPir sudo chmod 755 TX_DemoPir

sudo ./TX_DemoPir v a1 r3 i1000 t5 c1 f434 m100

In the silent folder there’s another version of the receiver demo code, with all the printf statements commented out and an exit(0) command immediately after it receives a valid code. We’ve done that so you can call the receiver code from a shell script, and when a valid message is received by the shell script you could send an email to your phone, or turn on an LED, or switch a relay controlling a water pump, or open a door lock.

cd silent
ls
RX_DemoPir.cpp | receiver with no message to screen, prints PIR2 and exits
receive.sh | shell script, prints “PIR 2 triggered” to console. Loops
receive2.sh | shell script, as above but doesn’t loop
receive3.sh | as above, and turns on LED connected to GPIO4 for 3 seconds.

To use the silent versions of the receiver

sudo g++ lwiringPi RX_Demo.cpp cc1100_raspi.cpp o RX_Demo sudo chmod 755 RX_Demo

chmod a+x receive3.sh
sudo ./receive3.sh

You can inspect & modify the contents of the source .cpp files and .sh files with nano. Example:

nano receive3.sh

You could use the TX_DemoPir program on several different Raspberry Pi’s, all with PIR modules attached and just modify the message sent to PIR1, PIR2, or PIR3 on each different Pi. Then on the receiver code, change this line, which currently looks for the number 2 → if( Rx_fifo[6] == 0x32) to look for PIR1 with 0x31 or look for PIR3 with 0x33.


Attach a PIR sensor to the transmitter Pi. If you pull the white dome off the Pir sensor you’ll usually see the pin designations screen-printed on the PCB.

Pir sensor | Raspberry Pi
VCC | 5 Volts
GND | GND
OUT | GPIO 4 (pin 7 in WiringPi speak)

If you’re attaching an LED to the receiver, attach a 220 ohm resistor in series, like this:

In the previous pages we mentioned how the CC1101 radio gets configured - to work on a certain frequency, modulation scheme and gain level - by a configuration block sent over the SPI interface. When you run the standard TX_Demo and RX_Demo examples the current configuration settings for Config Register and PaTable get printed to the terminal, like this:


If you edit the file cc1100_raspi.cpp you’ll see the config block for the -m100 modulation speed option. The defaults are 868MHZ, and we’ve used 434MHz in the example above, so it got changed around a bit:


Here’s the example of the PaTable settings (power output of the radio for each frequency)

You can see our PaTable setting matches the 433/434MHz setting from the command line
RX_Demo options.

Say you want to reverse engineer a wireless gadget of your own, and you’ve already descovered the frequency, modulation scheme and data rate, how do you then find out the correct config values for the radio? You need a free Windows application from Texas Instruments called Smart RF Studio 7.


You can download it from http://www.ti.com/tool/download/SMARTRFTM-STUDIO/

Then click the CC1101 button’s red circle and choose Open RF Device in Offline Mode.


The main screen for Smart RF Studio 7 looks like this:

In the center panel you can choose RF Parameters: Base Frequency, Modulation Format, Data Rate and TX Power. When you change these values, the hex values on the right of the screen change too. When all the options are set you can export the Hex values needed to configure the radio by clicking the Register Export button on the top right of the window.

I’ve chosen template RF settings, then clicked on Select in the Registers tab, moved all 61 values to the right hand pane, and then scrolled down to TEST0, selected everything below that starting with PARTNUM, and moved them back to the left pane. I’m then left with a block of 47 values that can be cut and pasted back into SpaceTeddy’s cc1100_raspi.cpp file, as replacements.

That only leaves us with the question of how do you discover that frequency, modulation scheme and data rate of your current RF devices, that you might want to make the CC1101 module receive from, or replicate the transmission signal of another device.

Say I have a wireless alarm system in my home that I know operates around the 868MHz band. I’d first get a USB RTL-SDR/TV dongle for around £10-£20 from eBay (search on eBay for RTL-SDR) and then install GQRX on my Ubuntu Linux PC following this short guide: http://gqrx.dk/download/install-ubuntu You also need to blacklist the kernel driver otherwise it assumes you want to use it as a TV stick – see http://oh2bsc.com/2015/02/17/getting-started-with-sdr-radio-using-dvb-t-usb-dongle-and-gqrx/ (http://oh2bsc.com/2015/02/17/getting-started-with-sdr-radio-using-dvb-t-usb-dongle-and-gqrx/)

GQRX is then installed to the Internet folder on my list of Programs.


In the picture above I’ve set the frequency to 868 MHz and clicked the play button in the top left. A waterfall display then scrolls down the screen and when any RF gadget transmits it appears in the waterfall. I pressed the keyfob for my car, and two red & yellow bursts appeared. Often 868MHz gadgets operate on FSK, and because two bursts appear at the same time, I’m assuming the modulation scheme is 2-FSK (supported by CC1101). We could export this sample to Audacity or InSpectrum to work out the data rate or we could use Universal Radio Hacker.

Universal Radio Hacker is a set of tools for capturing and analysing RF signals from an RTL-SDR USB dongle. Assuming you’ve tried GQRX, URH will run fine too.

https://github.com/jopohl/urh

The manual is here: https://github.com/jopohl/urh/raw/master/data/userguide.pdf

And the excellent YouTube tutorial videos start here: https://www.youtube.com/watch?v=kuubkTDAxwA (https://www.youtube.com/watch?v=kuubkTDAxwA)

I chose to run without installation, like this:

git clone https://github.com/jopohl/urh/
cd urh/src/urh
./main.py


If you want to do long range communications of say 1KM using two CC1101 modules, then you’ll need a pair of decent Yagi antennas and free space between the two sites. The antennas are £30 each from Farnell : http://uk.farnell.com/lprs/yagi-434a/antenna-yagi-7-element-434mhz/dp/2096215 or http://uk.farnell.com/lprs/yagi-869a/antenna-yagi-9-element-869-915mhz/dp/2096216

If you liked this PDF please follow @securipi on twitter.
Check out our website www.securipi.co.uk

We sell lots of electronic parts and kits for Raspberry Pi and Arduino in our eBay shop: http://stores.ebay.co.uk/ConvertStuffUK

and also here:

https://tri.co.uk/

If you spot any typos please email tim@trcomputers.co.uk

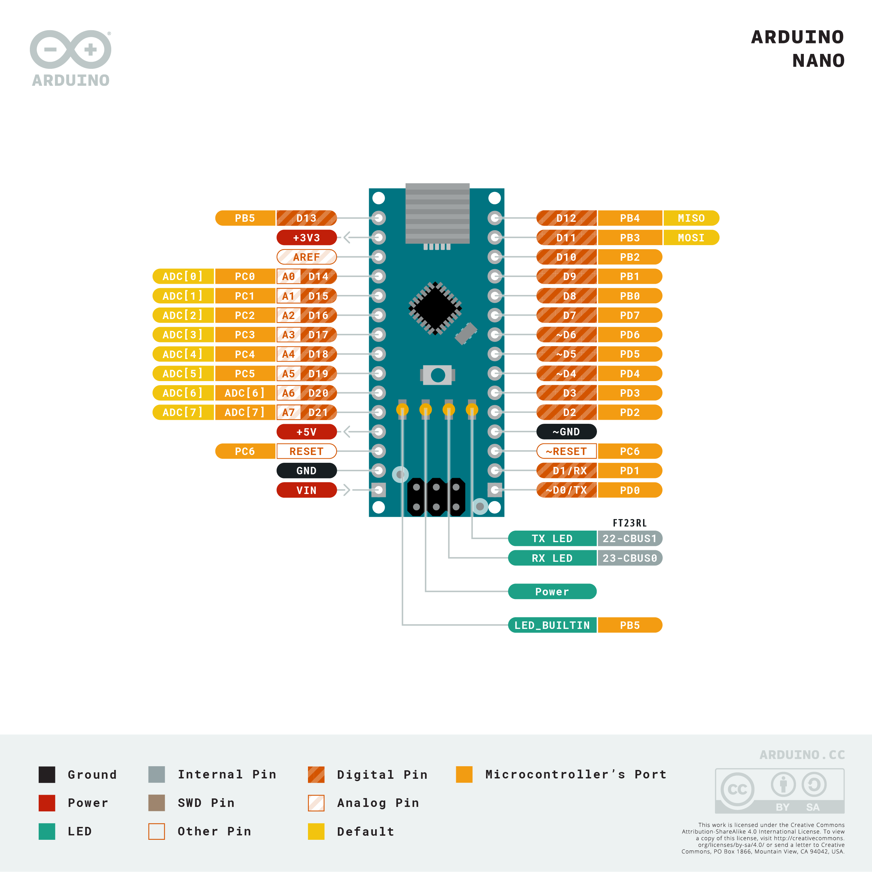
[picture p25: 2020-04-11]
doc/mcu/Pinout-NANO_latest.png

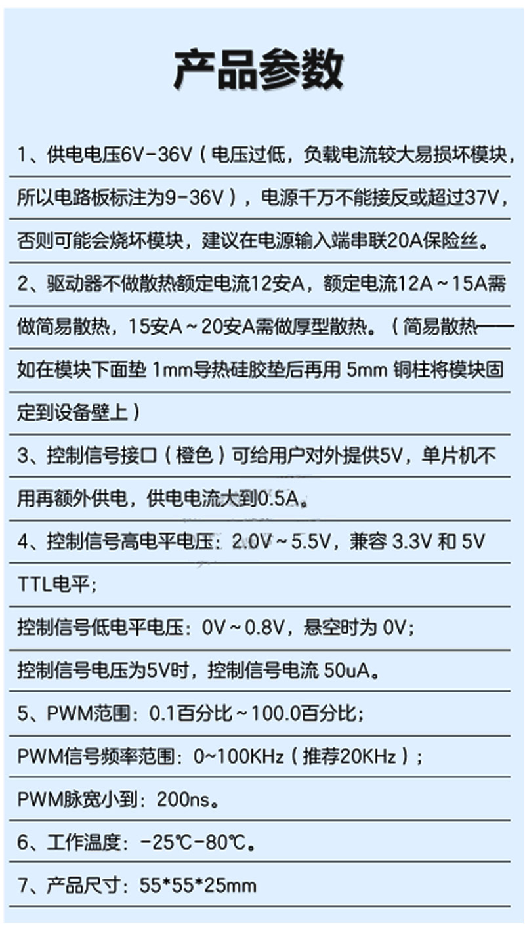
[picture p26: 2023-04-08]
doc/motor_driver/JZ3615_spec.jpg

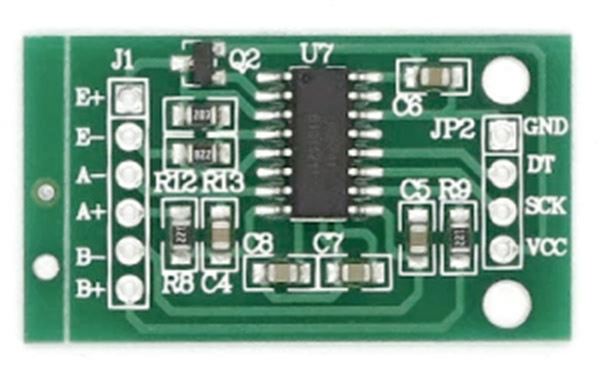
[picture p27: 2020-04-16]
doc/load_cell/HX711_module.jpg

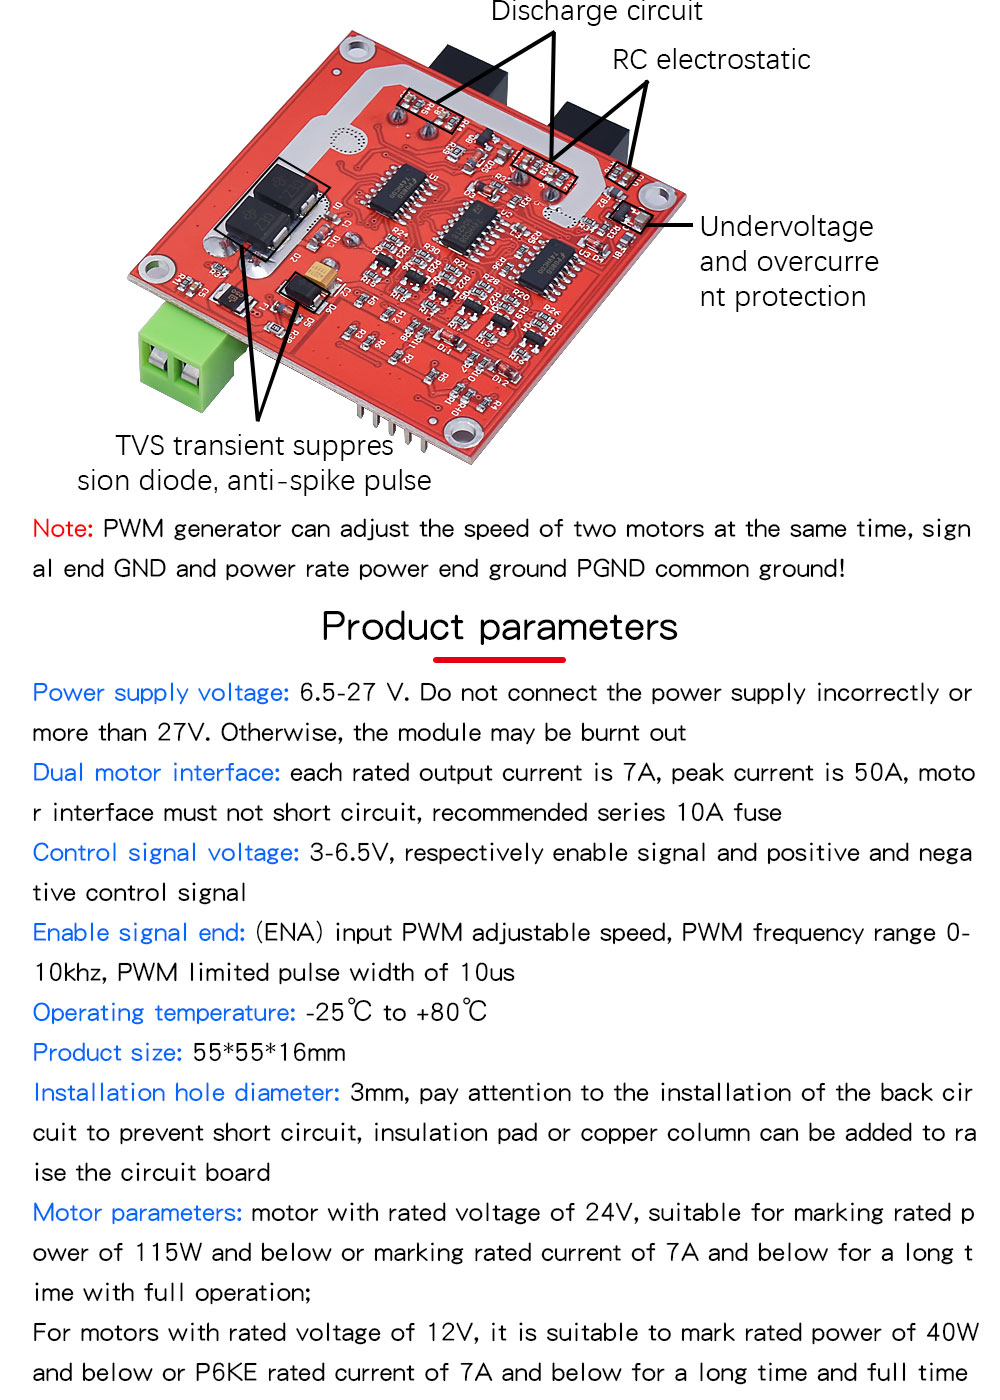
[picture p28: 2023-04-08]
doc/motor_driver/JZ3615_details3.jpg

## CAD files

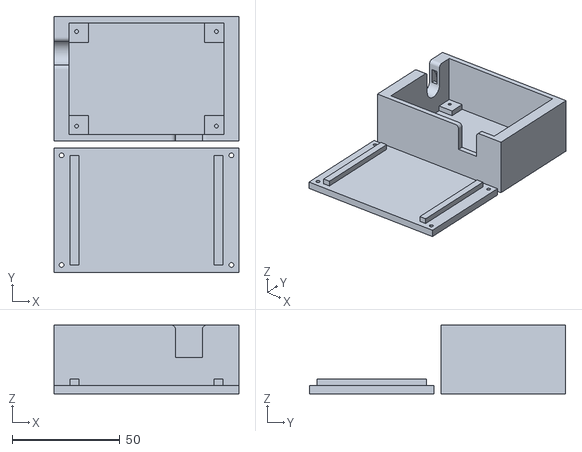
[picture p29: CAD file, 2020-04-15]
00_USBRadioDongle/PlasticCase/SimplePlasticCase.stl
86.0 x 119.1 x 32.0

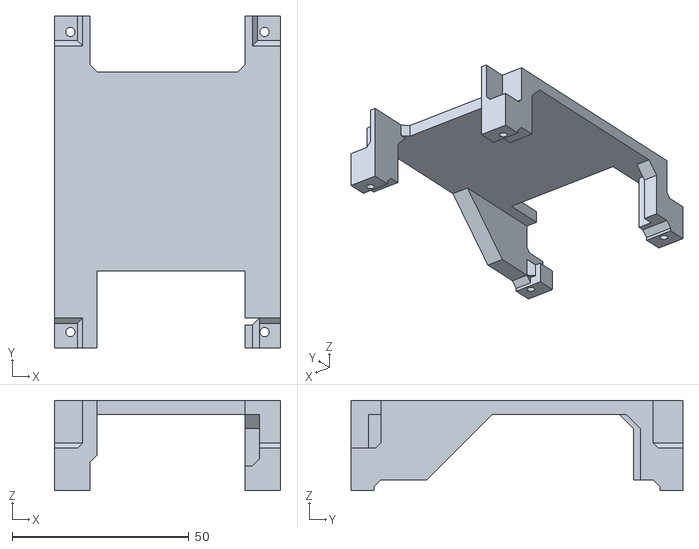
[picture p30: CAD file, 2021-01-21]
02_RadioPIDController/case/top.stl
64.0 x 94.0 x 25.5

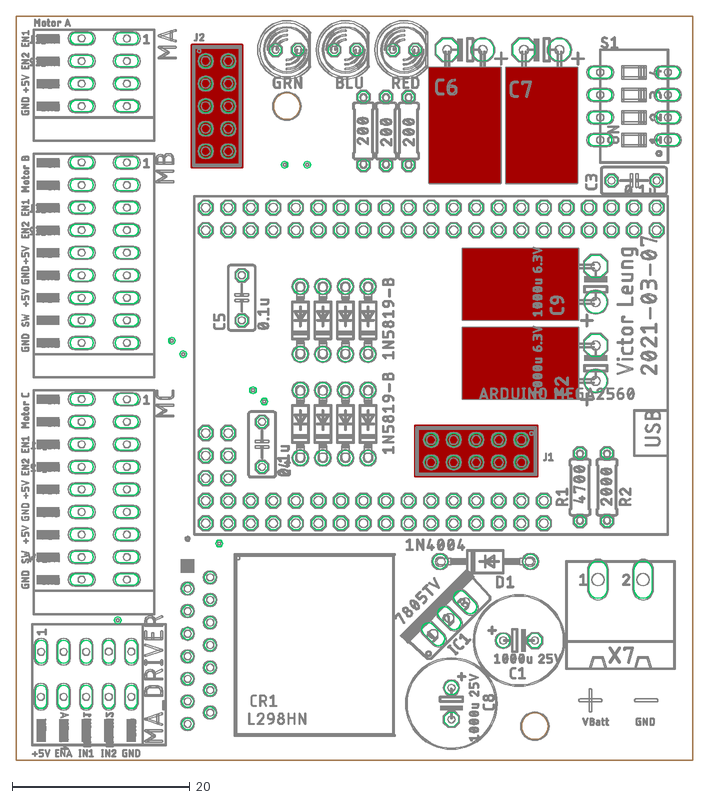
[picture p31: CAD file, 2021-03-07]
04_RadioPIDControllerV3/Controller.dxf
76.2 x 83.8

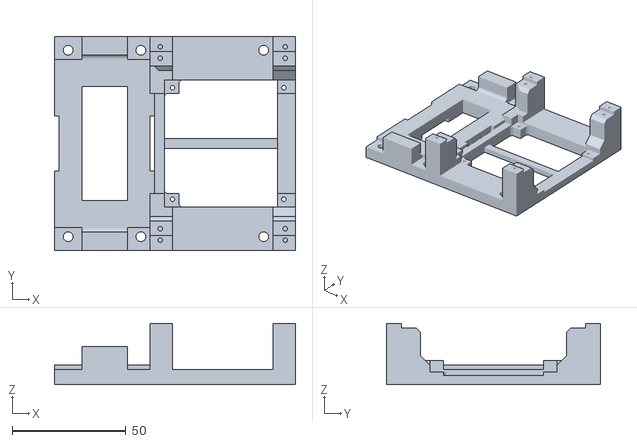
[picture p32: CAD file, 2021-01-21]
02_RadioPIDController/case/btm.stl
106.0 x 94.0 x 27.0

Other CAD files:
00_USBRadioDongle/PlasticCase/SimplePlasticCase.3dm
02_RadioPIDController/case/SeparateCase.3dm

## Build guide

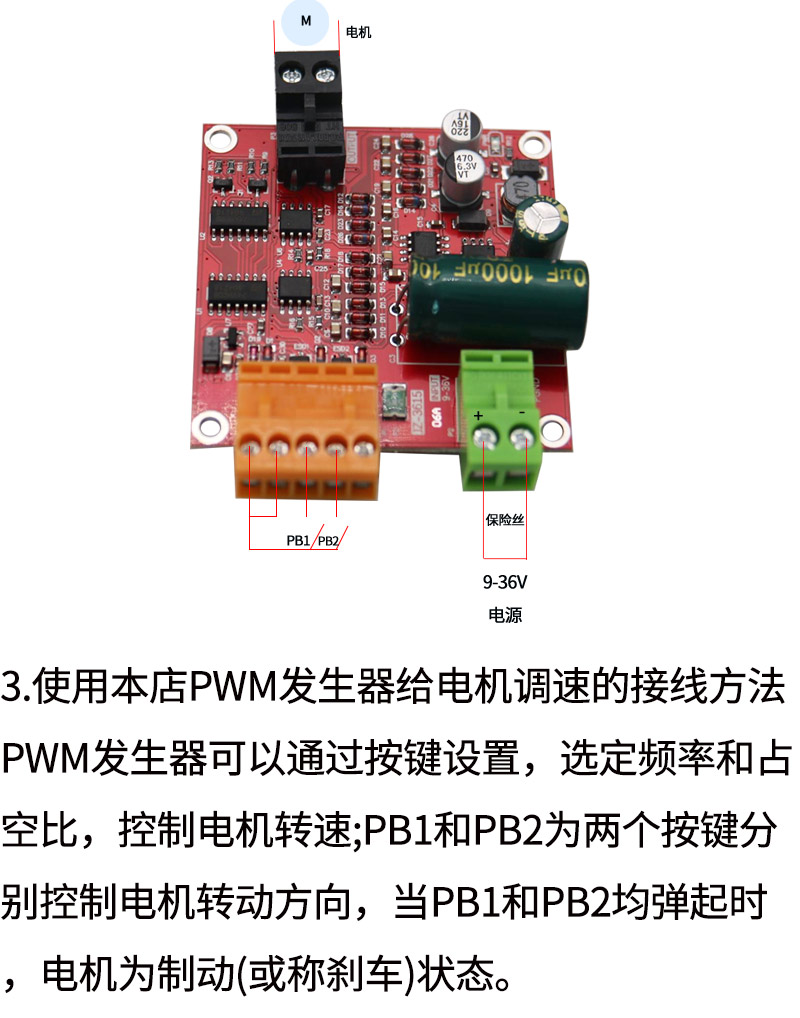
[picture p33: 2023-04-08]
doc/motor_driver/JZ3615_wiring2.jpg

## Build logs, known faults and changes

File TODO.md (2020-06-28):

# TODO

- [x] Document Radio Module
- [ ] Document First Clamp Controller
  - [ ] Schematic
  - [ ] Write up
  - [ ] Photo
- [x] Document Second Clamp Controller
  - [x] Schematic
  - [x] Write up
  - [x] Photo
- [ ] Clarify Motor Controller Direction Truth Table
- [ ] Photograph the two controllers
  - [ ] Controller 01 
  - [ ] Controller 02

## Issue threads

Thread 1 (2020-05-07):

7805 Linear Regulator is too inefficient causing short standby time.

yck011522, 2020-05-07:

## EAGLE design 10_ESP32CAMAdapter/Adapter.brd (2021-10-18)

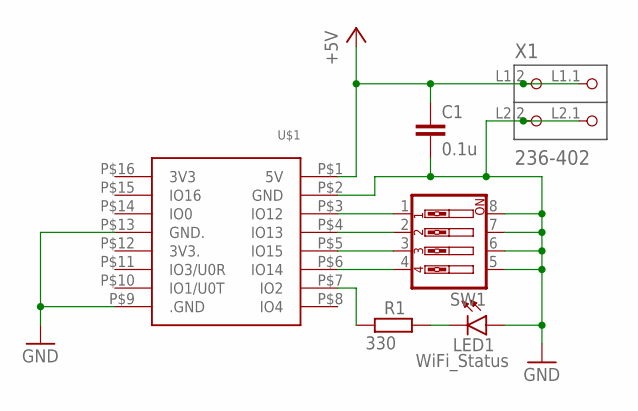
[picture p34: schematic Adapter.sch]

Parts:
C1: 0.1u; C050-030X075
LED1: WiFi_Status; LED3MM
R1: 330; 0204V
SW1: SW_DIP-4; EDG-04
U$1: ESP32-CAM
X1: 236-402; P-236-402

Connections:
+5V: C1.1, U$1.P$1 (5V), X1.L1.1 (P1.1), X1.L1.2 (P1.2)
GND: C1.2, LED1.A, SW1.5, SW1.6, SW1.7, SW1.8, U$1.P$2 (GND), U$1.P$9 (.GND), U$1.P$13 (GND.), X1.L2.1 (P2.1), X1.L2.2 (P2.2)
unnamed: SW1.1, U$1.P$3 (IO12)
unnamed: SW1.2, U$1.P$4 (IO13)
unnamed: SW1.3, U$1.P$5 (IO15)
unnamed: SW1.4, U$1.P$6 (IO14)
unnamed: R1.1, U$1.P$7 (IO2)
unnamed: LED1.K (C), R1.2

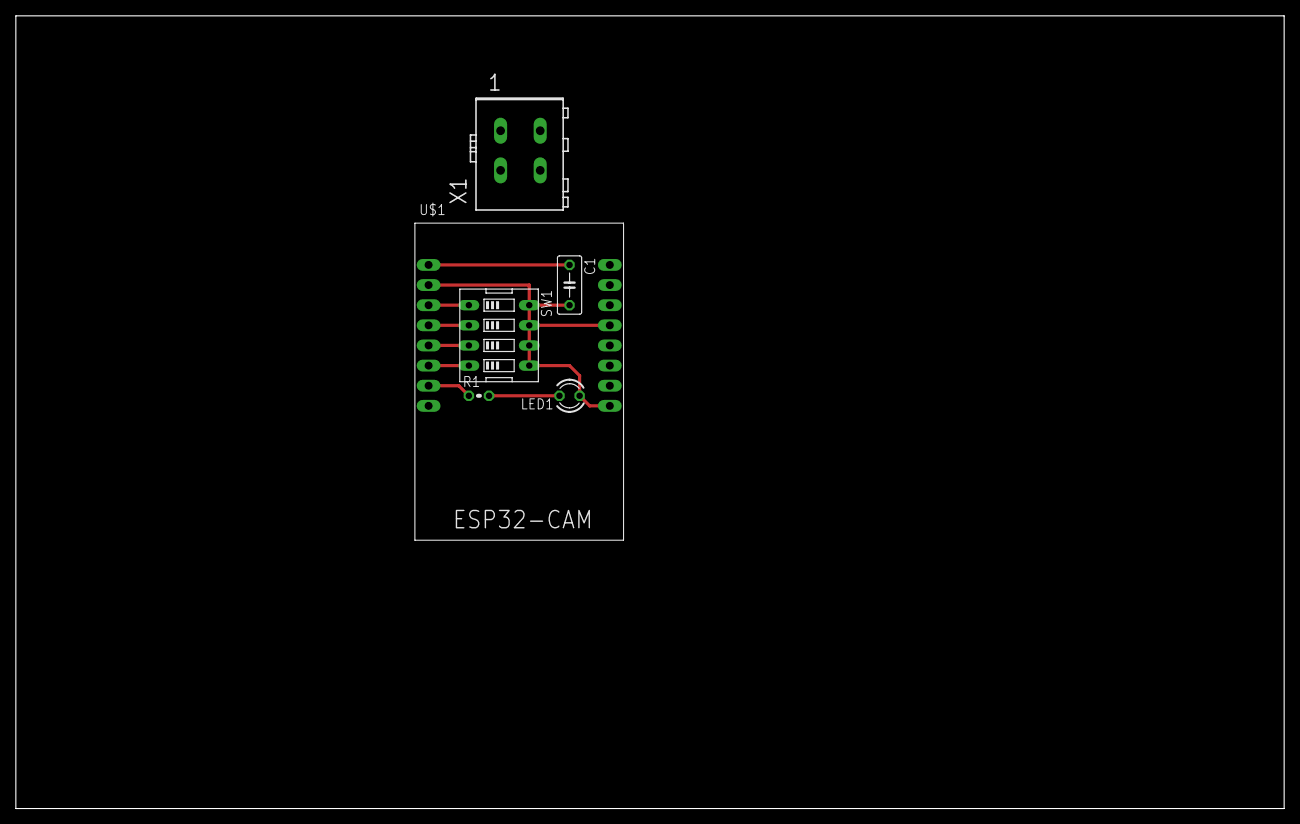
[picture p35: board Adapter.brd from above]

Board: 2 copper layers, 160.0 x 100.0 mm, 6 parts (0 on the bottom side), 8 nets.

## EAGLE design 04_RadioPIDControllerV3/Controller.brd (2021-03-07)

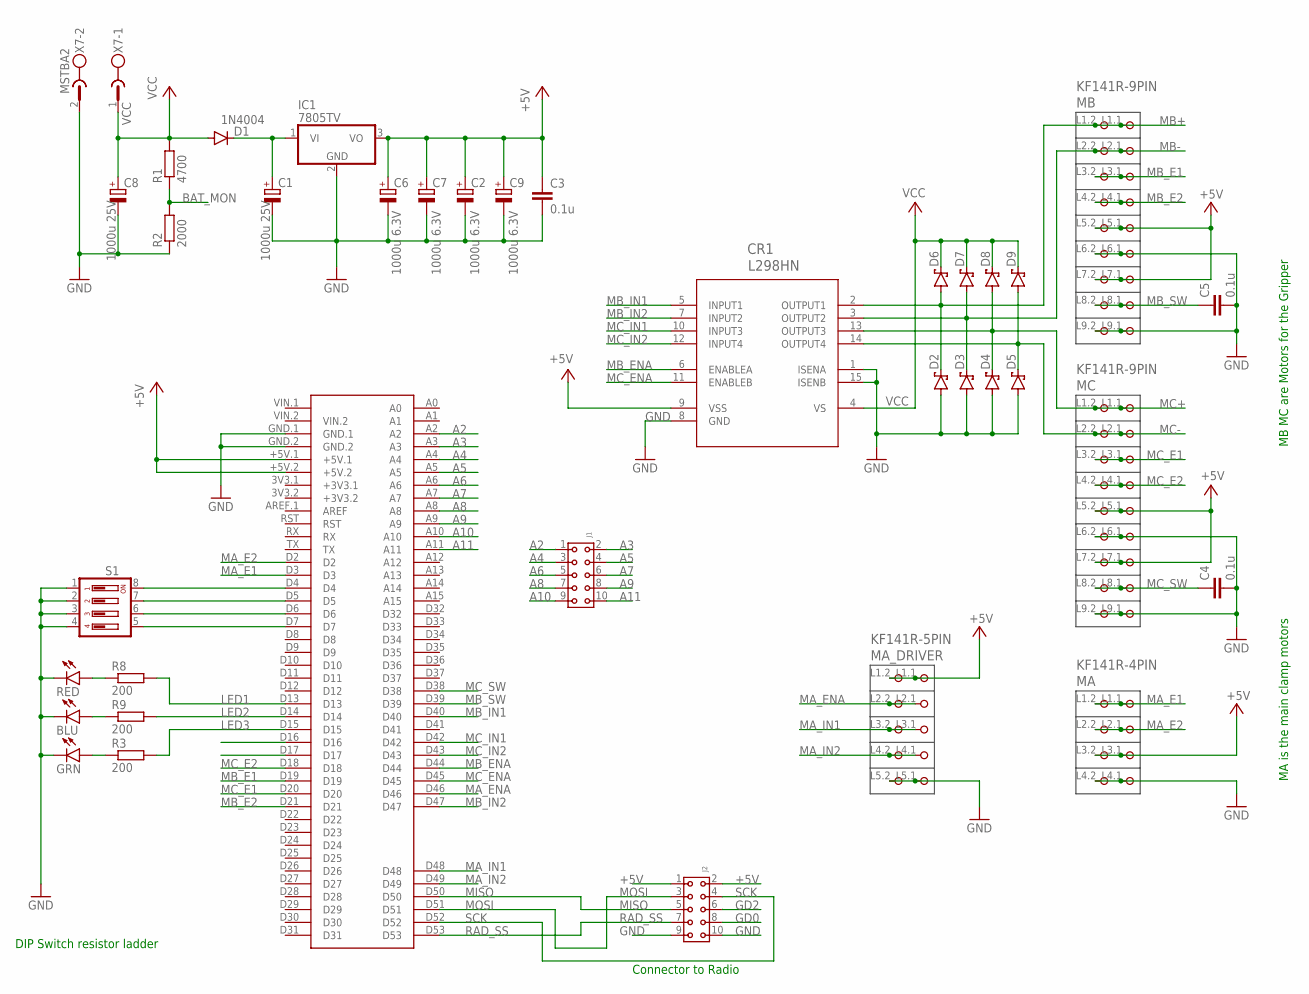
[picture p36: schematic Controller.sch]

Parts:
BLU: LED5MM
C1, C8: 1000u 25V; E3,5-10
C2, C6, C7, C9: 1000u 6.3V; E4-8-13HORI
C3, C4, C5: 0.1u; C050-030X075
CR1: L298HN; MULTIWATT15_H_STM
D1: 1N4004; DO41-10
D2, D3, D4, D5, D6, D7, D8, D9: 1N5819-B; DO41-7.6
GRN: LED5MM
IC1: 7805TV; TO220V
J1, J2: 6130XX21821_61301021821; 61301021821
MA: KF141R-4PIN
MA_DRIVER: KF141R-5PIN
MB: KF141R-9PIN
MC: KF141R-9PIN
R1: 4700; 0207/7
R2: 2000; 0207/7
R3, R8, R9: 200; 0207/7
RED: LED5MM
S1: DIP04YL
U$1: MEGA2560_MIKRO
X7: MSTBA2

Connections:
+5V: C2.+, C3.1, C6.+, C7.+, C9.+, CR1.9 (VSS), IC1.3 (VO), J2.1, J2.2, MA.L3.1 (P3.1), MA.L3.2 (P3.2), MA_DRIVER.L1.1 (P1.1), MA_DRIVER.L1.2 (P1.2), MB.L5.1 (P5.1), MB.L5.2 (P5.2), MB.L7.1 (P7.1), MB.L7.2 (P7.2), MC.L5.1 (P5.1), MC.L5.2 (P5.2), MC.L7.1 (P7.1), MC.L7.2 (P7.2), U$1.+5V.1, U$1.+5V.2
A2: J1.1, U$1.A2
A3: J1.2, U$1.A3
A4: J1.3, U$1.A4
A5: J1.4, U$1.A5
A6: J1.5, U$1.A6
A7: J1.6, U$1.A7
A8: J1.7, U$1.A8
A9: J1.8, U$1.A9
A10: J1.9, U$1.A10
A11: J1.10, U$1.A11
BAT_MON: R1.1, R2.2
GD0: J2.8
GD2: J2.6
GND: BLU.K (C), C1.-, C2.-, C3.2, C4.2, C5.2, C6.-, C7.-, C8.-, C9.-, CR1.1 (ISENA), CR1.8 (GND), CR1.15 (ISENB), D2.A, D3.A, D4.A, D5.A, GRN.K (C), IC1.2 (GND), J2.9, J2.10, MA.L4.1 (P4.1), MA.L4.2 (P4.2), MA_DRIVER.L5.1 (P5.1), MA_DRIVER.L5.2 (P5.2), MB.L6.1 (P6.1), MB.L6.2 (P6.2), MB.L9.1 (P9.1), MB.L9.2 (P9.2), MC.L6.1 (P6.1), MC.L6.2 (P6.2), MC.L9.1 (P9.1), MC.L9.2 (P9.2), R2.1, RED.K (C), S1.1, S1.2, S1.3, S1.4, U$1.GND.1, U$1.GND.2, X7.2
LED1: R8.2, U$1.D13
LED2: R9.2, U$1.D14
LED3: R3.2, U$1.D15
MA_E1: MA.L1.1 (P1.1), MA.L1.2 (P1.2), U$1.D3
MA_E2: MA.L2.1 (P2.1), MA.L2.2 (P2.2), U$1.D2
MA_ENA: MA_DRIVER.L2.1 (P2.1), MA_DRIVER.L2.2 (P2.2), U$1.D46
MA_IN1: MA_DRIVER.L3.1 (P3.1), MA_DRIVER.L3.2 (P3.2), U$1.D48
MA_IN2: MA_DRIVER.L4.1 (P4.1), MA_DRIVER.L4.2 (P4.2), U$1.D49
MB+: CR1.2 (OUTPUT1), D2.C, D6.A, MB.L1.1 (P1.1), MB.L1.2 (P1.2)
MB-: CR1.3 (OUTPUT2), D3.C, D7.A, MB.L2.1 (P2.1), MB.L2.2 (P2.2)
MB_E1: MB.L3.1 (P3.1), MB.L3.2 (P3.2), U$1.D19
MB_E2: MB.L4.1 (P4.1), MB.L4.2 (P4.2), U$1.D21
MB_ENA: CR1.6 (ENABLEA), U$1.D44
MB_IN1: CR1.5 (INPUT1), U$1.D40
MB_IN2: CR1.7 (INPUT2), U$1.D47
MB_SW: C5.1, MB.L8.1 (P8.1), MB.L8.2 (P8.2), U$1.D39
MC+: CR1.13 (OUTPUT3), D4.C, D8.A, MC.L1.1 (P1.1), MC.L1.2 (P1.2)
MC-: CR1.14 (OUTPUT4), D5.C, D9.A, MC.L2.1 (P2.1), MC.L2.2 (P2.2)
MC_E1: MC.L3.1 (P3.1), MC.L3.2 (P3.2), U$1.D20
MC_E2: MC.L4.1 (P4.1), MC.L4.2 (P4.2), U$1.D18
MC_ENA: CR1.11 (ENABLEB), U$1.D45
MC_IN1: CR1.10 (INPUT3), U$1.D42
MC_IN2: CR1.12 (INPUT4), U$1.D43
MC_SW: C4.1, MC.L8.1 (P8.1), MC.L8.2 (P8.2), U$1.D38
MISO: J2.5, U$1.D50
MOSI: J2.3, U$1.D51
unnamed: C1.+, D1.C, IC1.1 (VI)
unnamed: R8.1, RED.A
unnamed: BLU.A, R9.1
unnamed: GRN.A, R3.1
unnamed: S1.8, U$1.D4
unnamed: S1.7, U$1.D5
unnamed: S1.6, U$1.D6
unnamed: S1.5, U$1.D7
RAD_SS: J2.7, U$1.D53
SCK: J2.4, U$1.D52
VCC: C8.+, CR1.4 (VS), D1.A, D6.C, D7.C, D8.C, D9.C, R1.2, X7.1

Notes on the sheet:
Connector to Radio
DIP Switch resistor ladder
MB MC are Motors for the Gripper
MA is the main clamp motors

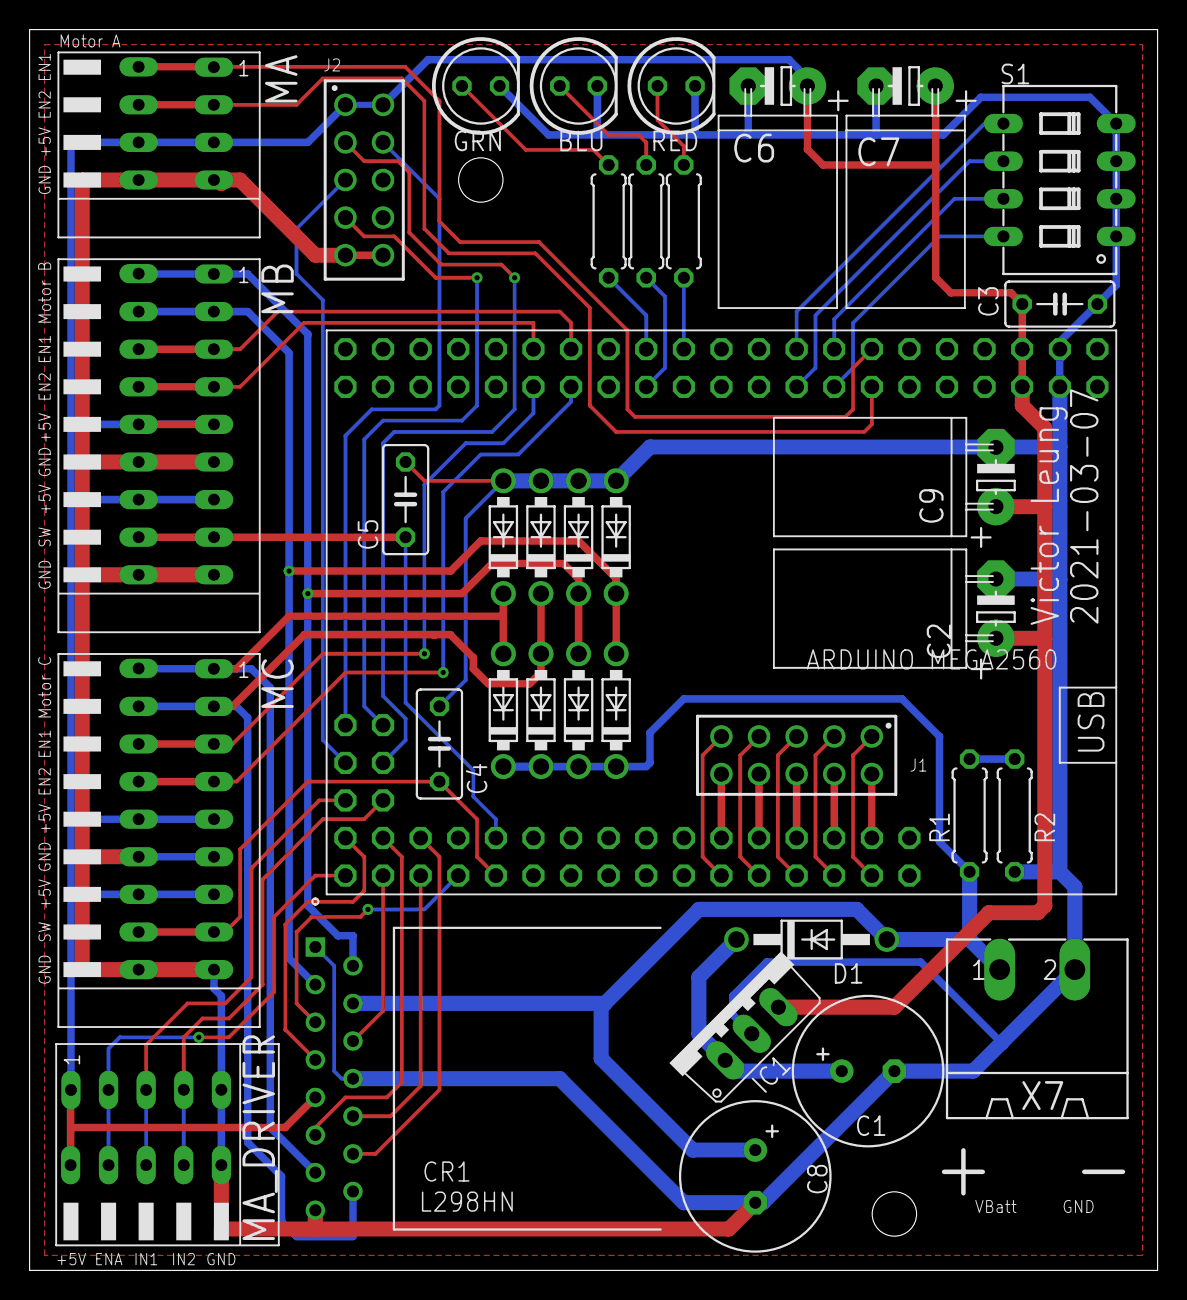
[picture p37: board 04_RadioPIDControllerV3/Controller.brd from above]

Board: 2 copper layers, 76.2 x 83.8 mm, 37 parts (0 on the bottom side), 50 nets.

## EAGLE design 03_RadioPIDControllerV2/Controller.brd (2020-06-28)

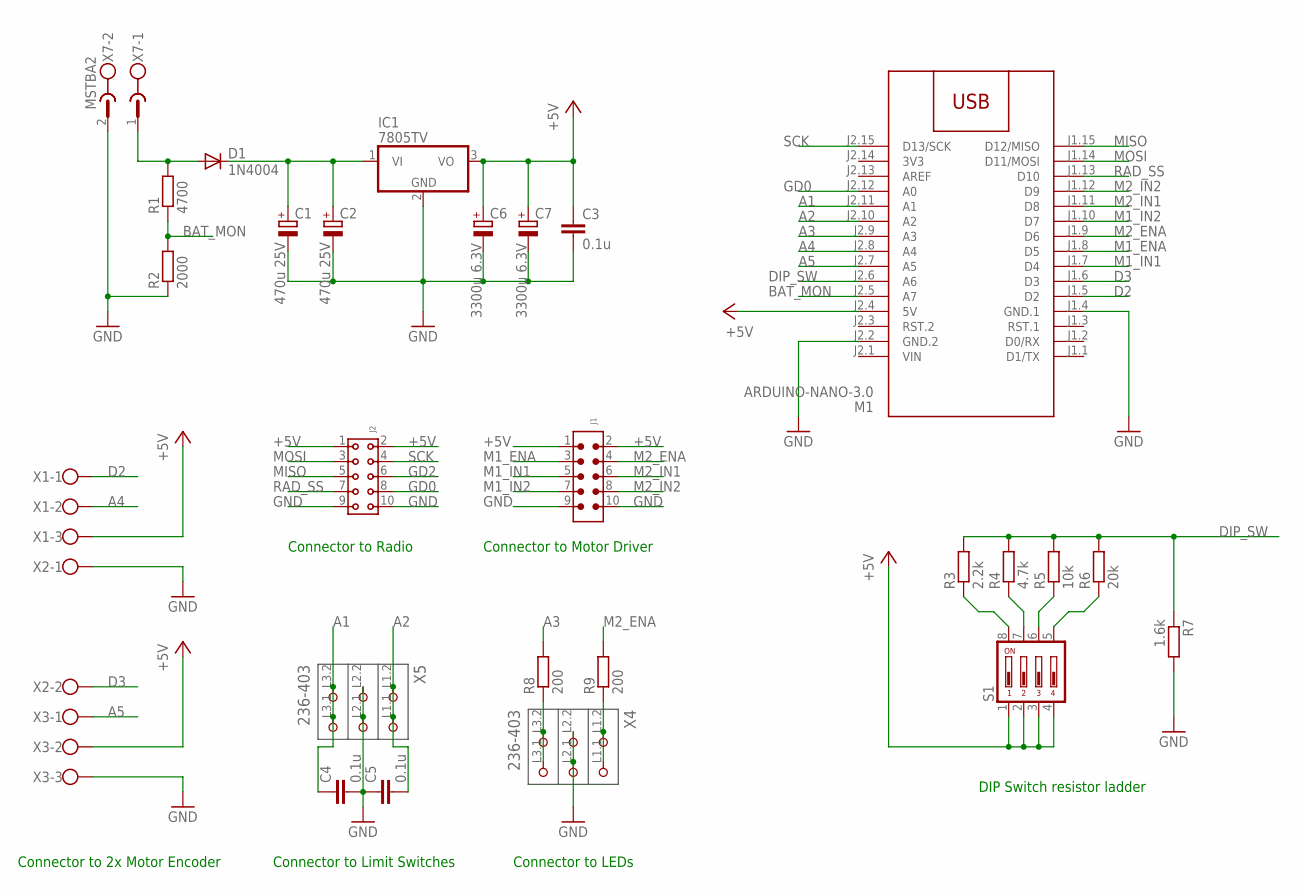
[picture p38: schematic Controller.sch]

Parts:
C1, C2: 470u 25V; E3,5-8
C3, C4, C5: 0.1u; C050-030X075
C6, C7: 3300u 6.3V; E3,5-10
D1: 1N4004; DO41-10
IC1: 7805TV; TO220V
J1: 6120XX21621_61201021621; 61201021621
J2: 6130XX21821_61301021821; 61301021821
M1: ARDUINO-NANO-3.0
R1: 4700; 0207/10
R2: 2000; 0207/7
R3: 2.2k; 0207/10
R4: 4.7k; 0207/10
R5: 10k; 0207/10
R6: 20k; 0207/10
R7: 1.6k; 0207/10
R8: 200; 0207/12
R9: 200; 0207/15
S1: DIP04YL
X1, X3: W237-103
X2: W237-102
X4, X5: 236-403; P-236-403
X7: MSTBA2

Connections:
3V3: M1.J2.14 (3V3)
+5V: C3.1, C6.+, C7.+, IC1.3 (VO), J1.1, J1.2, J2.1, J2.2, M1.J2.4 (5V), S1.1, S1.2, S1.3, S1.4, X1.3, X3.2
A1: C4.1, M1.J2.11 (A1), X5.L3.1 (P3.1), X5.L3.2 (P3.2)
A2: C5.2, M1.J2.10 (A2), X5.L1.1 (P1.1), X5.L1.2 (P1.2)
A3: M1.J2.9 (A3), R8.2
A4: M1.J2.8 (A4), X1.2
A5: M1.J2.7 (A5), X3.1
BAT_MON: M1.J2.5 (A7), R1.1, R2.2
D2: M1.J1.5 (D2), X1.1
D3: M1.J1.6 (D3), X2.2
DIP_SW: M1.J2.6 (A6), R3.2, R4.2, R5.2, R6.2, R7.1
GD0: J2.8, M1.J2.12 (A0)
GD2: J2.6
GND: C1.-, C2.-, C3.2, C4.2, C5.1, C6.-, C7.-, IC1.2 (GND), J1.9, J1.10, J2.9, J2.10, M1.J1.4 (GND.1), M1.J2.2 (GND.2), R2.1, R7.2, X2.1, X3.3, X4.L2.1 (P2.1), X4.L2.2 (P2.2), X5.L2.1 (P2.1), X5.L2.2 (P2.2), X7.2
M1_ENA: J1.3, M1.J1.8 (D5)
M1_IN1: J1.5, M1.J1.7 (D4)
M1_IN2: J1.7, M1.J1.10 (D7)
M2_ENA: J1.4, M1.J1.9 (D6), R9.2
M2_IN1: J1.6, M1.J1.11 (D8)
M2_IN2: J1.8, M1.J1.12 (D9)
MISO: J2.5, M1.J1.15 (D12/MISO)
MOSI: J2.3, M1.J1.14 (D11/MOSI)
unnamed: D1.A, R1.2, X7.1
unnamed: R8.1, X4.L3.1 (P3.1), X4.L3.2 (P3.2)
unnamed: C1.+, C2.+, D1.C, IC1.1 (VI)
unnamed: R4.1, S1.7
unnamed: R5.1, S1.6
unnamed: R6.1, S1.5
unnamed: R3.1, S1.8
unnamed: R9.1, X4.L1.1 (P1.1), X4.L1.2 (P1.2)
RAD_SS: J2.7, M1.J1.13 (D10)
SCK: J2.4, M1.J2.15 (D13/SCK)
VIN: M1.J2.1 (VIN)

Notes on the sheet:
Connector to Motor Driver
Connector to Radio
Connector to 2x Motor Encoder
DIP Switch resistor ladder
Connector to LEDs
Connector to Limit Switches

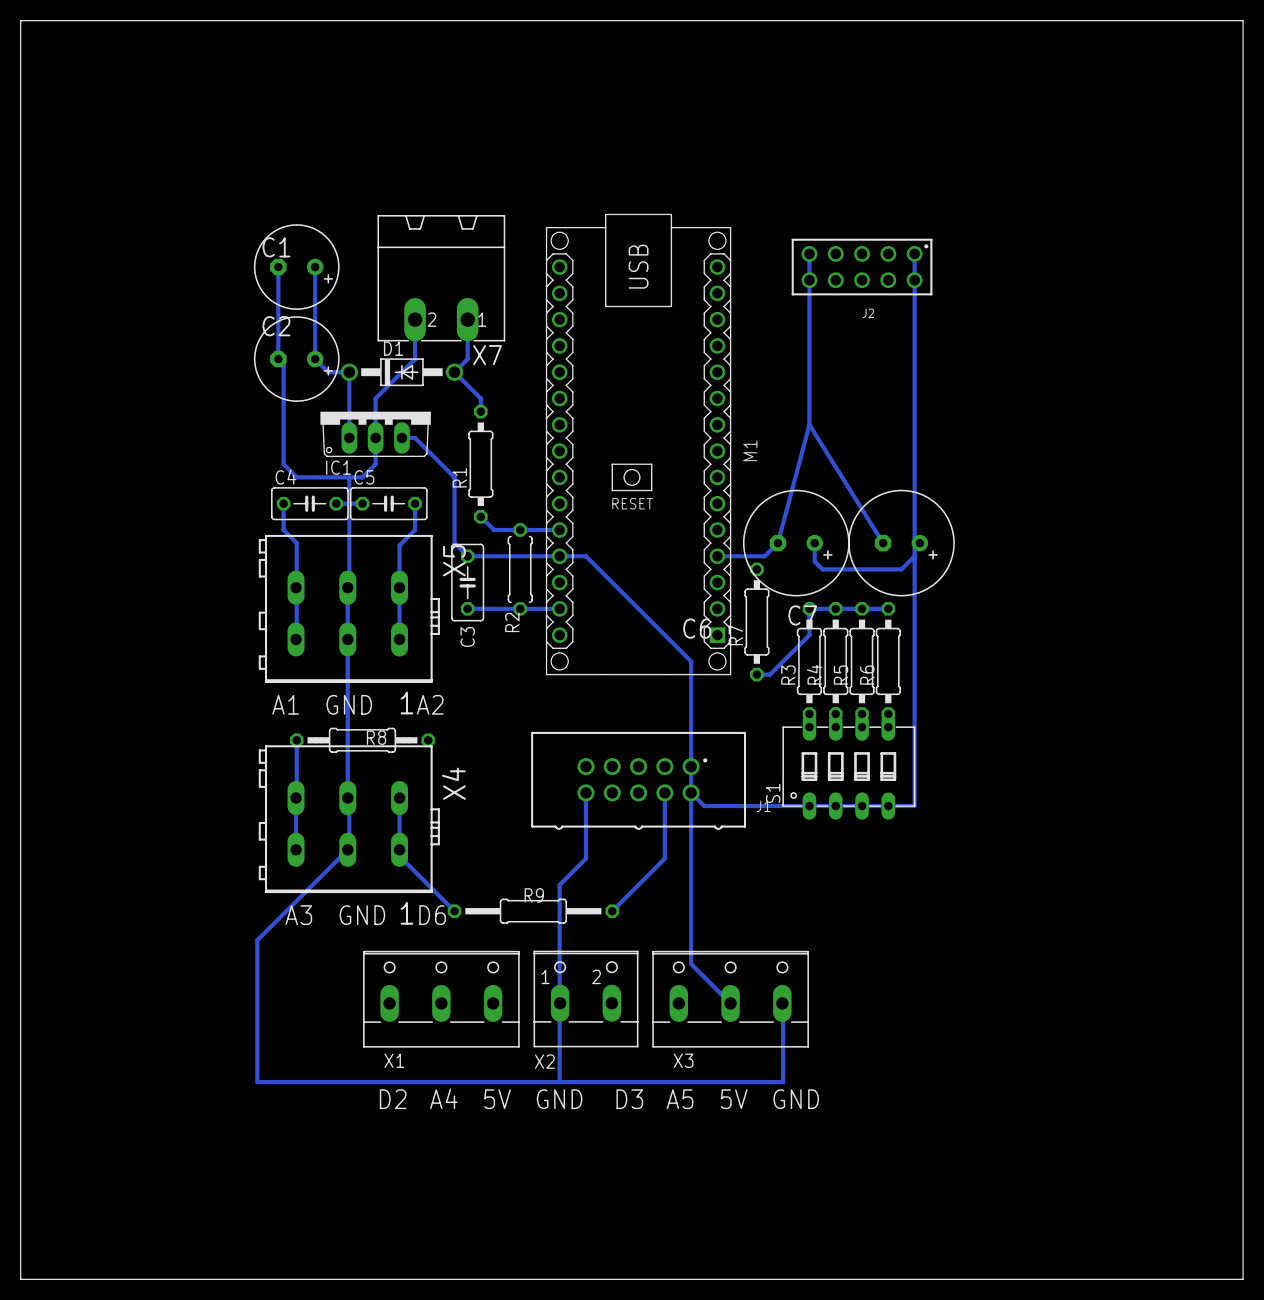
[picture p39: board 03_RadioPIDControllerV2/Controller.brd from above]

Board: 2 copper layers, 118.1 x 121.6 mm, 28 parts (0 on the bottom side), 30 nets.

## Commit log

2020-04-10 Migrated a lot of docs to this repo
    [LM7805_solutions.sch, untitled.brd, untitled.sch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]
2020-04-11 Doc for radio and controller 2
    [Controller.brd, Controller.sch, ResistorLadderCalculator.xlsx]
2020-04-15 Plastic case
    [SimplePlasticCase.3dm, SimplePlasticCase.stl]
2020-04-16 Added Radio Dongle Doc
    [Dongle.sch]
2020-04-16 Added documentation for 01 Serial Controller
    [SerialController.sch]
2020-06-28 Added Doc of Controller 03
    [Controller.brd, Controller.sch]
2021-01-21 Case for the PID Controller board used for motor testing
    [SeparateCase.3dm, btm.stl, top.stl]
2021-01-21 USB Dongle plastic case
    [SimplePlasticCase.3dm]
2021-03-07 04 PID Controller with 2 extra motor
    [Controller.brd, Controller.dxf, Controller.sch]
2021-05-01 Board error log
2021-10-18 Added Adapter board related to #2
    [Adapter.brd, Adapter.sch]

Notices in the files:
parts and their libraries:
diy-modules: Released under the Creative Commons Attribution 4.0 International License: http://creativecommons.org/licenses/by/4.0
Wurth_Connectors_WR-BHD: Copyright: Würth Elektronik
